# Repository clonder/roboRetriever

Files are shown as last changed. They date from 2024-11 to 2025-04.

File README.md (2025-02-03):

# 🐾 Robo Retriever

https://github.com/user-attachments/assets/8c03f9e1-ced2-4b13-8463-932fbea5f0ad

---

## 🧾 Project Description

This project aims to develop **Robo Retriever**, a four-legged robotic dog controlled via Wi-Fi, to explore and demonstrate principles of computer architecture. Using a microcontroller, we will program the robot to execute movement commands, leveraging instruction cycles, control signals, and memory management techniques. By building and testing the robot, our team will gain hands-on experience with embedded systems, hardware interfacing, and real-time data processing.

---

## 📢 Project Information

- **References**:
  - [ESP32 Small Robot Dog on Instructables](https://www.instructables.com/ESP32-Small-Robot-Dog/)
  - [PCBWay Quadruped Robot Model Introduction](https://www.pcbway.com/project/shareproject/An_introduction_to_quadruped_robot_models_0f4aa139.html)

---

## 📦 Components

| **Name** | **Description** | **Amount** | **Price** | **Link** |
|---|---|---|---|---|
| Servo Motors | Motors for robot leg movement | 12 | 60CHF | [Amazon Link](https://www.amazon.de/-/en/dp/B09WQYPP17?_encoding=UTF8&th=1) |
| Timing Belts | 25cm belts for leg motion | 4 | 6CHF | [Amazon Link](https://www.amazon.com/Cyrank-Printer-Accessories-Synchronous-MendelMax/dp/B0CH17YFQL) |
| ESP32 | Microcontroller for control | 1 | 15CHF | [Amazon Link](https://www.amazon.de/-/en/diymore-Nodemcu-Development-Bluetooth-2-ESP32/dp/B0D9BTQRYT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) |
| Battery (Akku) | Powers ESP32 and servos | 1 | - | [Amazon Link]() |
| Servo Shield | Connects ESP32 to servos and distributes power | 1 | - | [Servo Shield Link](https://www.pcbway.com/project/shareproject/Multiple_Servo_Motor_Controller_Board_DOIT_ESP32_DEVKIT_V1_c9c8165e.html) |
| Micro USB Cable | For flashing and programming ESP32 | 1 | - | We have this |
| Non-slip Material  | Rubber or pads to keep feet stable | 4 | - | [Amazon Link]() |
| Filament | 3D printing filament | 2kg | - | [Bambulab Link](https://eu.store.bambulab.com/en-ch) |
| Screws | M3 screws in various lengths | As needed  | - | [Schraubenking.ch](https://www.schraubenking.ch/) |
| Ruthex Inserts | Inserts for securing screws | As needed  | - | No need to buy |
| Delivery | For all the items, just sum | As needed  | 15CHF | - | No need to buy |

---

For more details look at the report.

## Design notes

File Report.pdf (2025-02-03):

Universität Basel, 21.01.2025

# RoboRetriever - quadruped robot

Anastasiya Merkushova, Jiri Käser, Mathieu Groenen, Rahel Kempf Lecture "Computer Architecture" by Prof. Dr. Christian Tschudin, HS24

Abstract
In this project, our aim was to build a walking quadruped robot that can be controlled via Wi-Fi. Our four-legged robot is able to walk using servo motors and an ESP32 microcontroller. The project involved designing a 3D model of the robot and printing it, determining the circuit design and power supply, and programming the servos for the robot’s movement. The robot is capable of basic movements such as tilting, walking, standing up, and sitting down.
1. Introduction
Inspired by Boston Dynamics’ Spot and other developments in quadruped robotics, we set out to create our own quadruped robot, driven by curiosity and a desire to explore the possibilities of four-legged locomotion. This project aims to design, develop, and build a quadruped robot from the ground up, from mechanical design and electronics to inverse kinematics and programming.

Quadruped robots are interesting because they are much more agile than their wheeled counterparts. Research shows their potential in traversing uneven terrain, recovering from falls and more. To remain realistic in the scope and ambitions for our project, we set out simple and hopefully achievable goals. Our goal was to build a robot that could stand up and walk.

In this report, we will delve into our journey to achieve these goals, beginning with the 3d design, in which we had to develop mechanics that would support the movements of our robot. We also had to choose an appropriate PCB design to control 12 servos at once and supply these servos with enough power. For the leg movement, we had to calculate the inverse kinematics and implement them in our code. Finally, to be able to remotely control the robot, we had to implement WIFI connection.

2. 3D Design
In this section, we will discuss the process of designing and testing the 3D model of our robot, as well as the challenges we encountered.

2.1 Physical design
First, we had to get the mental image of the robot moving. To provide our robot with the potential to turn, walk, and stand up we decided to go with three servos per leg, giving it three degrees of freedom.

To understand successful quadruped robot designs, we compared different examples online. In the end, we decided to position the servos in a way that minimizes movement, stabilizing the robot’s center of mass. This should simplify programming because we could neglect the factor of mass shifting, though it adds complexity to the mechanical design, requiring precision belts to transfer motion to the lower leg.

2.2 Model
Once the initial design was envisioned, we needed to model it in 3D software, print it, and test it excessively. For modelling, we used Onshape, a lightweight, browser-based 3D modelling software.

2.2.1 Upper and Lower Leg Design
We first modelled the upper and lower legs, along with the knee connection using a bearing. This was done very early on so we didn’t yet have the servos as reference, to check if the part would fit. Once the servos arrived, we tested the model. The initial design had several minor defects: the servo didn’t fit, there was insufficient space for a gear to be places between servo shaft and enclosure, the screw holes and the bearing hole were too small, and the strength of the part in general was too low. The final design is shown in Figure 1.

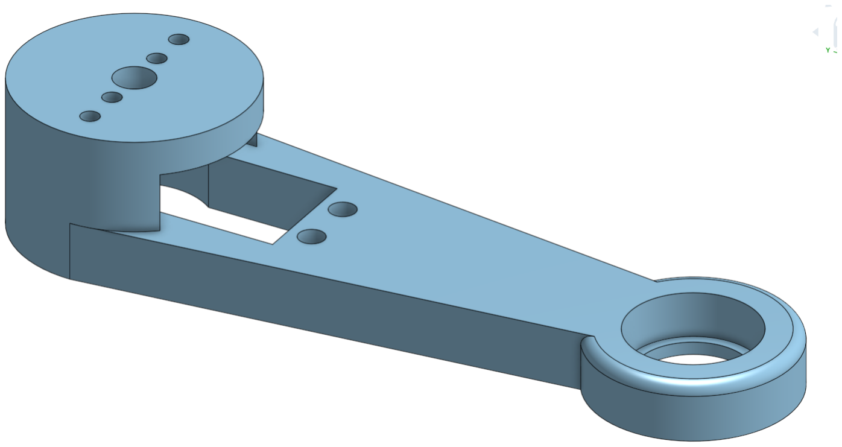
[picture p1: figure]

Figure 1. Final version of the upper leg

The lower leg had less issues but there were still a few. Issues were addressed by iterating between adjusting the 3D model according to the problems noticed during testing, reprinting and testing again. The final version of the lower leg can be seen in Figure 2.

2

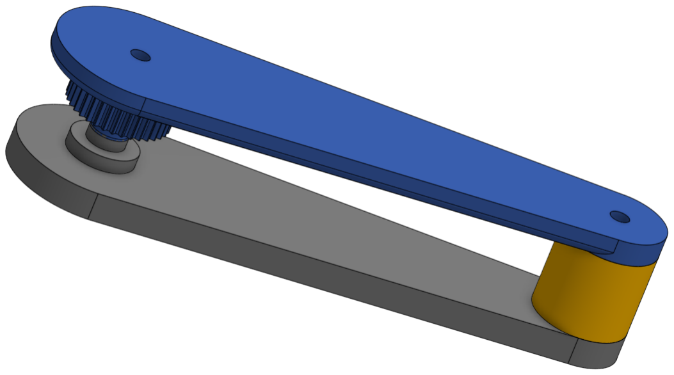
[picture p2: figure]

Figure 2. Final version of the lower leg

2.2.2 Lower Leg Motion
The next part that was addressed was the gear to drive the belt and therefore the motion of the lower leg. This part faced three main challenges: the gear needed to be compact yet strong enough to support several kilos of force, ensure the belt stayed securely in place, and have the correct gear ratio for optimal timing belt grip while keeping the height minimal.

To ensure strength, the print options were set to 6 wall layers, 50% infill, and a 0.4mm nozzle. To resolve the height issue, a new part was designed to position the servo slightly farther out, providing the extra millimeters needed for proper gear placement. Gear teeth were refined by printing 10 gears with varying teeth counts, testing, and repeating with finer increments until the optimal 35-tooth gear was selected. The final design is shown in Figure 3.

Figure 3. Final design of the gear

The final issue was belt tensioning, for which no ideal solution was found. The process went as follows:

1. A piece of timing belt was tensioned by hand hard enough not to slip any more
2. Marks for the loop closure, cut point, and overlap for sewing were added.
3. Three to four holes were punched into the belt
4. The belt was sewn together by hand with nylon string

This was the most painstaking and annoying process of assembling the robot since a little to less or too much tension meant to repeat the four steps above and they took around 20-30 minutes to complete. In the end we managed to get only two out of four running perfectly. The others worked but slipped when too much force was exerted on them. This had to then be reworked when we were in the programming phase.

2.2.3 Shoulder Design
The last two pieces needed were the shoulder, that would hold the servo rotating the upper leg and the main body holding the servos that rotate the shoulder and the electronics. The shoulder was rather straight forward as it simple needed to include a mount for the servo controlling the upper leg and a couple of holes to allow for the main body servos to control the shoulder. There were a couple of issues still, the most problematic being that one threaded insert hole was too large which caused one part of the shoulder to be ripped out during the programming phase. The final design of the shoulder can be seen in Figure 4.

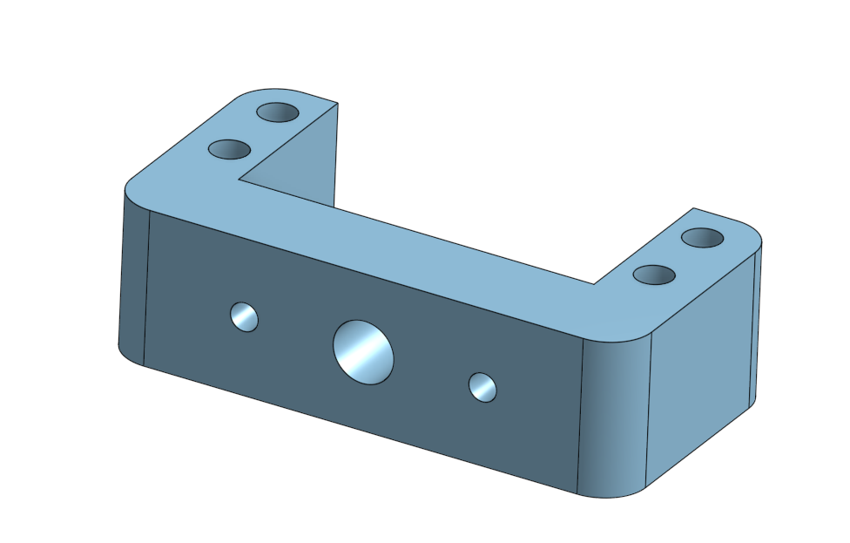
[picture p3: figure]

Figure 4. Final design of the shoulder

2.2.4 Body Design
The main body also caused a bunch of issues. We potentially wanted to power the robot by a lithium ion battery, therefore there had to be space for this, then the electronics needed to be fixed in space to make sure that cables don’t come loose easily and it needed four servo mounts while at the same time staying as light as possible. For the battery mount simply a hole in the floor was made and therefore it can be taped below the center of the main body. For the electronic mount four pillars were designed, that would hold one screw each. The problem with those was that when inserting the ruthexes these pillars would deform easily due to the low heat resistant nature of PLA Filament which made it extremely difficult to keep the correct distances for the electronic mount. The final part can be seen in figure 5.

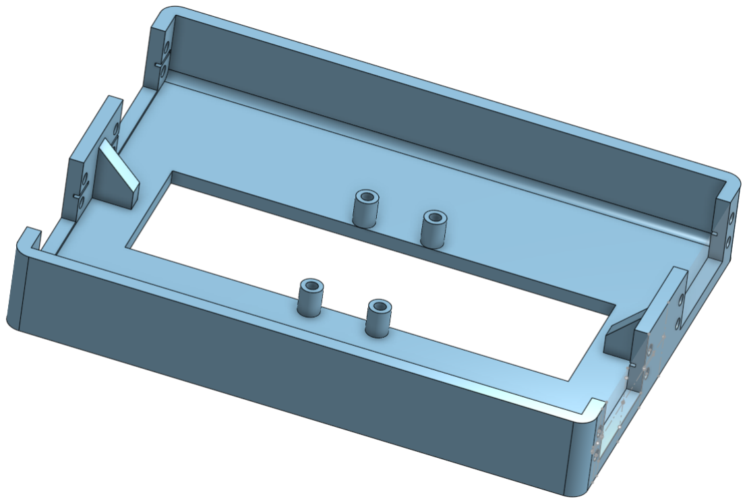
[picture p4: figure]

Figure 5. Final design of the main body

3. Electronic design
One of the core challenges in building a quadruped robot is the need to manage multiple servo motors simultaneously. The hexagonal PCB design, shown in Figure 6, was chosen

Universität Basel | 3

because it is designed to control up to 16 servo motorsa
This PCB accommodates an ESP32 microcontroller (ESP32-WROOM-32 DevKit V1b
), which features built-in Wi-Fi capabilities and allows for seamless control of the robot’s operations. The ESP32 can be powered through its USB port (5V), VIN pin, or its 3.3V regulator.

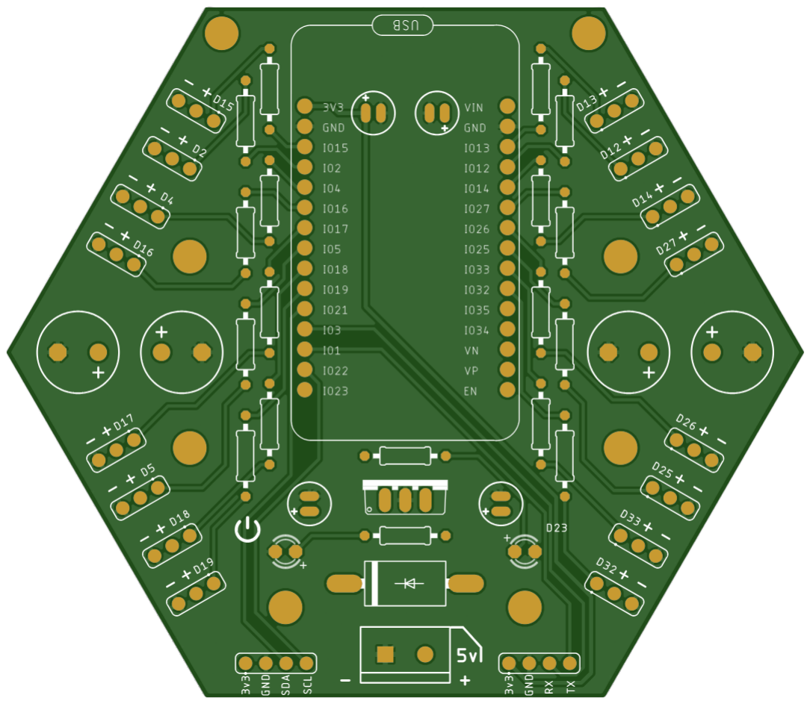
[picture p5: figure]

Figure 6. Hexagonal PCB design for servo motor control

3.1 PCB and Power
The PCB was assembled with the necessary components, including connectors, resistors, and capacitors. For the robot, we used 12 servo motors (DIYmore DM996 model), which operate at a voltage range of 4.8 V to 6.0 V, with optimal performance at 6.0 V.

Since the ESP32 operates at 5V using VIN pin, and the motors perform optimally at 6V, we opted to power the ESP32 directly via USB. For the servo motors, we used two power supplies connected in parallel: a 3-channel 5 V supply rated at 4 A and a single-channel 5 V supply rated at 4 A, providing a total current capacity of 8 A. This setup provided sufficient power to meet the robot’s peak requirements, as each servo motor has a peak current draw of 500 mA.

4. Inverse Kinematics
In this part, we explore the calculations needed for the inverse kinematics of the robot. Inverse kinematics works by choosing the location of the leg specified by its coordinates (x, y, z) and calculating the angles needed to move the leg to these coordinates. The complete leg movement is thus described by the function (θh, θs, θw) = Fθ(x, y, z). Our calculations are based on the calculations described in the OpenQuadruped project c
, with some changes made
due to differing leg design.
a. PCB design (https://www.pcbway.com/project/shareproject/Multiple_Servo_Motor_Controller_Board_DOIT_ESP32_DEVKIT_V1_c9c8165e.html)
b. ESP32 Pinout Reference (https://lastminuteengineers.com/esp32-pinout-reference/)
c. https://www.adhamelarabawy.com/images/IK_Model.pdf

4.1 Derivation
In general, we know the coordinates x, y, z which are specified by the starting condition. Additionally, SL (Shoulder length), UL (Upper leg) and LL (Lower leg) are given.

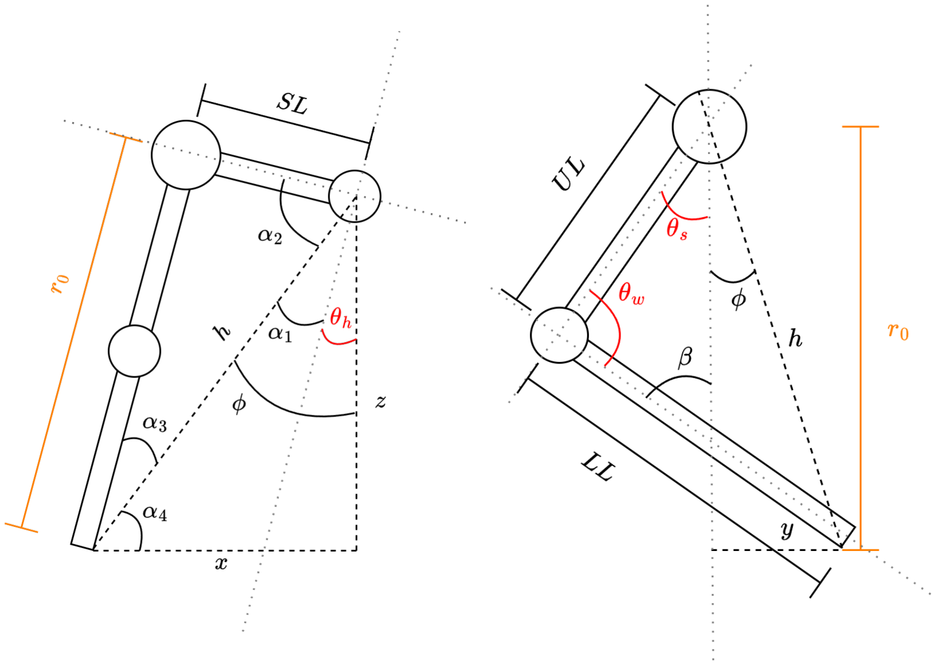
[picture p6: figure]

Figure 7. Front (left) and Side (right) view of the leg

First we look at the derivation of the θh angle as seen in figure 7, which is the angle between the body and the leg. We first calculate the distance r0.

h =

p
x

2 + z

2 ⇒ r0 =

p
h

2 − SL² =

p
x

2 + z

2 − SL²

The different angles are then given as

α2 = arccos
SL
h

α1 =

π
2

− α2

ϕ = arctan x
z

Which then gives

⇒ θh = ϕ − α1 = arctan x
z
−

π
2

+ arccos
SL
h

Now for the side view as seen in figure 7 we have

ϕ = arctan
y
r0

h =

q
r

2
0 + y

2

For θs, the shoulder angle, using the cosine law we get

cos(θs + ϕ) = UL² + h

2 − LL²
2UL · h
⇒ θs = arccos

UL² + h

2 − LL²
2UL · h

− arctan
y
r0

For θw, the knee angle, using again the cosine law

cos(θw) = UL² + LL² − h

2
2UL · LL
⇒ θw = arccos

UL² + LL² − h

2
2UL · LL

4

Thus, we get formulas for all the needed angles fully dependent on the variables x, y, z, SL, UL and LL.

Because of the design and implementation, the leg has three degrees of freedom, as depicted in figure 8. With our calculations, we are enabled to freely position the robot’s leg based on its coordinates.

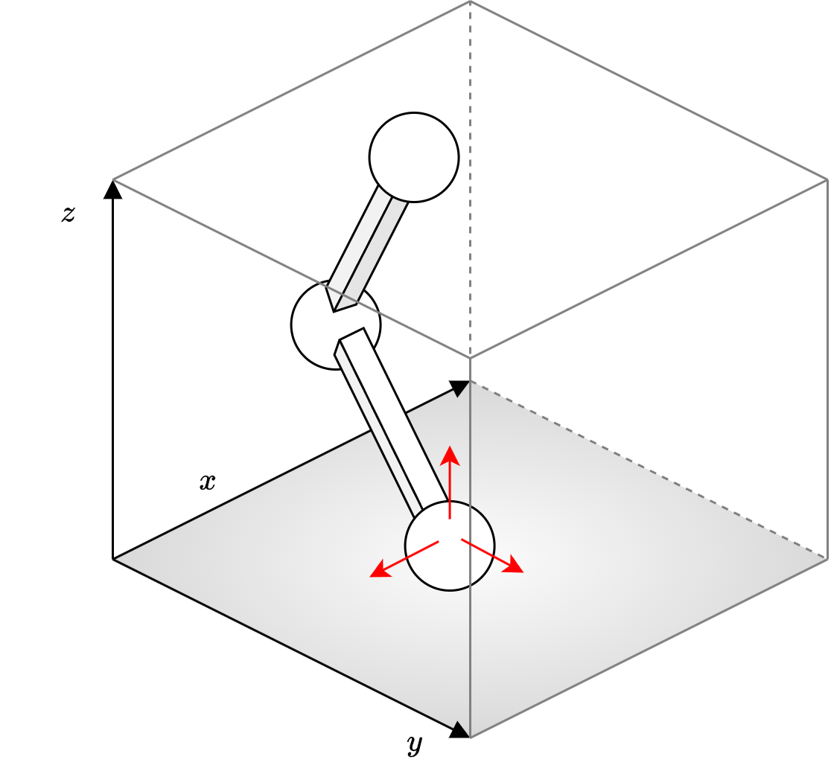
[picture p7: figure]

Figure 8. Degrees of freedom of the robot leg

5. Implementation
For programming we used an ESP32 Microcontroller, Platform.io and C++. In this section, we explain how we implemented the robot’s movements and the user interface.

5.1 Servo Positioning and Calibration
For the controlling of the servos, we use the ESP32Servo library.d The servos on the left and right side are mirroring each other, so the right side moves clockwise, while the left side moves counterclockwise. For the default positions, we had to take into consideration, that servos are only able to rotate 180 degrees. For the right side, both knee and shoulder servos are set to a default value of 0 degrees, while on the left side the default value is 180 degrees. This allows the servos on both sides to perform movements in the same range.

A large amount of time was spent correctly setting the servo angles and the positions of the legs. The need for calibration was important, as the Inverse Kinematics calculations required the correct initial placement. An offset in this placement would cause the leg to move not correct or not at all. The reason for this time-consuming part was because each time the legs needed to be recalibrated, the legs needed to be disassembled, adjusted and retested.

5.2 Movement
In this section, we describe some basic movements that the robot is capable of and how these movements are implemented. Figure 9 depicts the general architecture.
d. https://github.com/madhephaestus/ESP32Servo

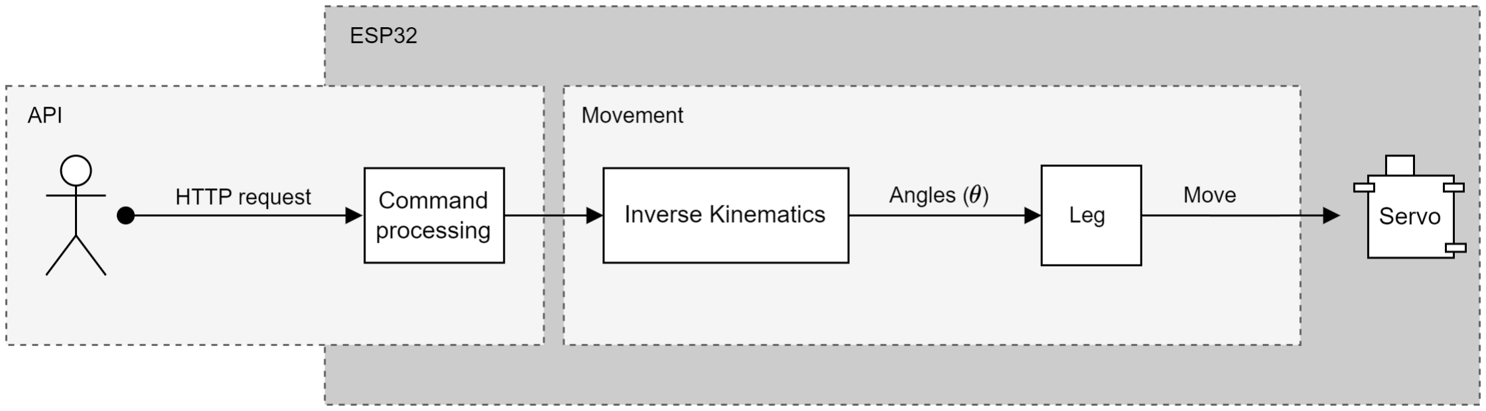
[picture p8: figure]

Figure 9. Code Architecture

5.2.1 Standing up
The robot can stand up by changing the z coordinate. The angles for this movement are calculated as described in chapter 4. With our default angles, the robot can go from 6 to 19 centimeters in height.

Standing up turned out to be harder than anticipated, as it not only depends on the correctly programmed movement but also on the stability and mechanical movement of the robot. During development, this caused a lot of problems due to the high tension and weight on the knee belts. A too quick movement of the legs would cause the knee to buckle under its own weight and would cause the robot to fall into itself. To solve this, we adjusted the movement to be incremental, such that the robot slowly moves upwards instead of one quick motion.

5.2.2 Tilting
To move the robot at an angle α in the side view (see the right image in 10) we need to specify the wanted x, y and z coordinates for each leg and based on these coordinates, calculate the needed angles. The only coordinate that changes in this movement is the z coordinate, i.e. the height of the robot.

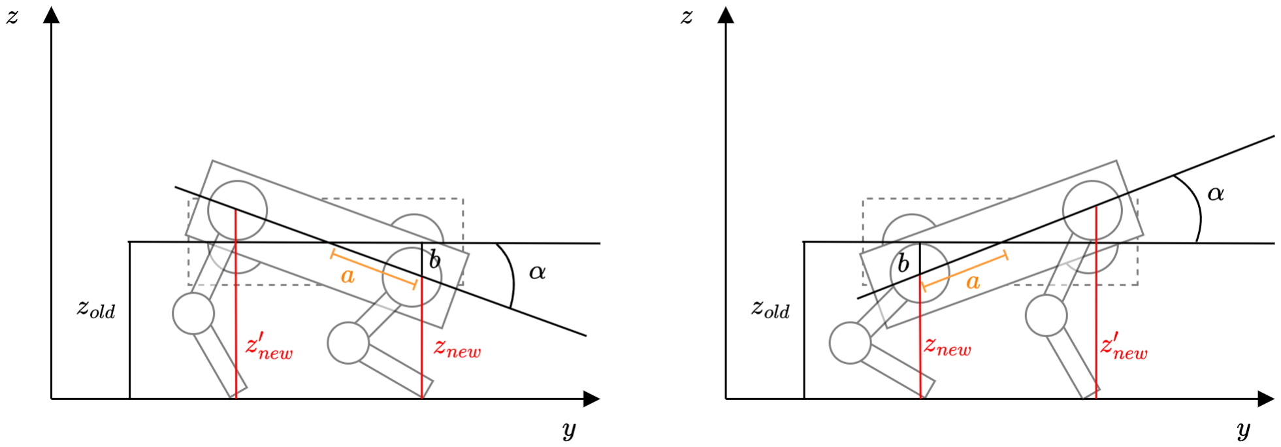
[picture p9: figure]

Figure 10. Side view of body tilting movement

b = a sin(α)

⇒znew = zold − b
⇒z

′
new = zold + b

We can then calculate the new angles for each leg. For the hind leg, the angle calculation becomes (θ

′
h

, θ′
s

, θ′
w) =
Fθ(x, y, znew) and the front legs (θ

′
h

, θ′
s

, θ′

w) = Fθ(x, y, z′
new).

5.2.3 Walking
To be able to walk, the robot needs to not only move the leg forward, but lift it up from the ground. For the

Universität Basel | 5

walking motion, we implement a parametrized curve.

γ1(t) =
t
0.05t

2

; −3 ≤ t < 3

γ2(t) =
| t − 6

1.281 cos(t − 6) + 1.718
; 3 ≤ t ≤ 9

The curves γ1(t) and γ2(t) then together define the walking motion of the robot, which can be seen in figure 11. The legs move along this curve clockwise. This curve was discretized, and the robot leg moves along the points in a certain timeframe. The leg starts at y = 0, moves clockwise and completes the movement in one iteration.

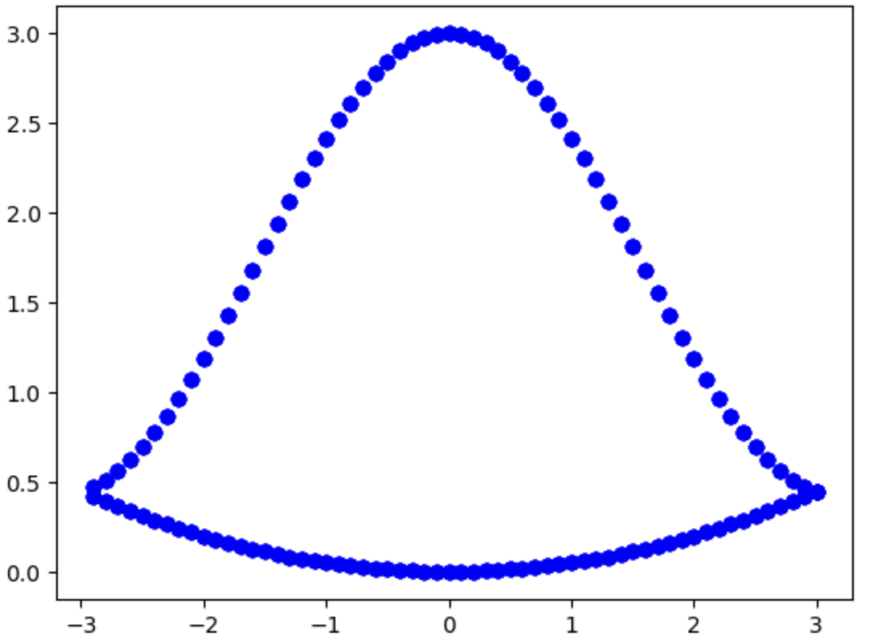
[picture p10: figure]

Figure 11. Parametrized curve of walking motion

It is important to note, that while the walking motion has been tested and works, there are still issues with the robot holding itself up due to improper balance.

5.3 User Interface
The robot’s control interface is implemented through a WiFi-enabled web server running on the ESP32 microcontroller. The system creates a wireless access point that allows for remote control of the robot’s movements via HTTP requests. Multiple commands can be chained together using semicolon separators, enabling complex movement sequences. The system implements automatic Wi-Fi reconnection and error handling to ensure reliable operation during extended use.

Table 1. Command Table

Command | Value | Function
z | 6-19 (cm) | Move vertically
y | -19-19 (cm) | Move forward/backward
bt | Angle | Tilt backward
ft | Angle | Tilt forward
w | Steps | Walk x steps forward
6. Conclusion
Our team successfully tackled an ambitious and engaging project. We gained valuable knowledge in quadruped robotics, electronics, and servo programming. Despite various challenges, we successfully completed our project and created a robot capable of executing basic commands, including walking.

6.1 Future Work
For future iterations of this project, several improvements could be implemented:
Power Supply: It would be beneficial to replace the current setup with a rechargeable battery for improved portability.
Mechanical Design: The printed parts could be revised to improve stability, and optimizing weight distribution would enhance the robot’s performance. Additionally, upgrading to wider belts with better tension mechanisms would support the robot’s weight more effectively. Software: Implementing additional movement commands would expand the robot’s capabilities and allow for more complex actions.
Project Management: Developing a more detailed project timeline, with careful consideration of dependencies between phases, would improve the project flow.

6.2 Division of Labor
Together we started planning the project, researched the topic, and decided on the required components. We distributed the work evenly, with each team member having specific areas of responsibility as outlined below. All team members contributed to the robot’s assembly and testing phases.
Anastasiya: PCB soldering, Wi-Fi interface
Jiri: 3D model design and development
Mathieu: Inverse kinematics calculations, leg movement programming
Rahel: Robot leg movement programming, Calibration

Appendix
Images
All figures depicted in this project report were self made. The 3D models are screenshots from during the design model. All other graphs were made using draw.io.

Material
All the most relevant materials used in the project can be found below
1. ESP32 WROOM 32 [Link] (https://www.amazon.de/-/en/diymore-Nodemcu-Development-Bluetooth-2-ESP32/dp/B0D9BTQRYT?nsdOptOutParam=true)
2. ESP32 Servo Control PCB [Link] (https://www.pcbway.com/project/shareproject/Multiple_Servo_Motor_Controller_Board_DOIT_ESP32_DEVKIT_V1_c9c8165e.html)
3. Servo motors [Link] (https://www.amazon.de/-/en/diymore-Gearbox-Helicopter-Aeroplane-Suitable/dp/B09WQYPP17?nsdOptOutParam=true)
4. Timing Belt [Link] (https://www.amazon.de/-/en/SIENOC-GT2-6-Open-Timing-Printer/dp/B06XX75JLV?nsdOptOutParam=true)
5. 3D fillament [Link] (https://eu.store.bambulab.com/en-ch/collections/pla/products/pla-basic-filament?variant=43923829129435)
6. Nylon string
7. Screws
8. Electrical parts (Resistors, Capacitors, Cables, Headers)

Code
All the relevant code can be found on the github repository.e All code was self-written, and ChatGPT was used as an additional tool to help with optimization and debugging of the code.
e. https://github.com/clonder/roboRetriever

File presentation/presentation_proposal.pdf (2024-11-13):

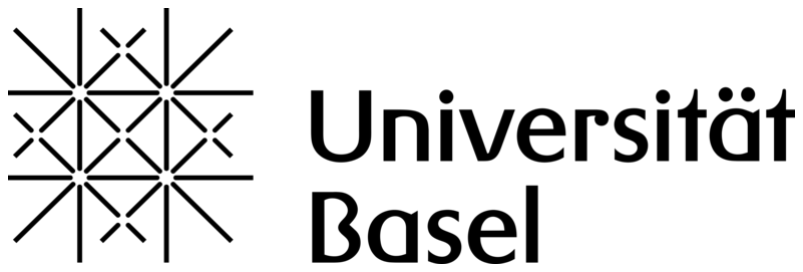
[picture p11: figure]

# Project Proposal Robo Retriever

## Computer Architecture

### A. Merkushova, J. Käser, M. Groenen, R. Kempf

Fall 2024

# Aim and goals

### - Aim:

- Develop a quadruped four-legged robotic pet controlled via Wi-Fi

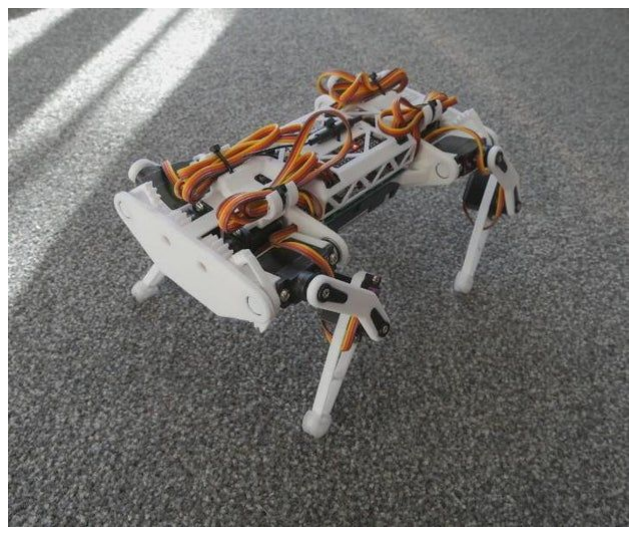
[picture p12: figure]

- Goals:
- Design Part and CAD Modeling
- 3D Printing of Parts
- Assembly
- Programming and Implementation

# Requirements

## Requirements

- ESP 32 - 38 pin with Wifi and Bluetooth
- BreadBoard / PCB
- 12 Servo Motors for movement
- Battery Holder / Batteries for power
- 3D Printing for casing

Hardware

- C / C++ for robot control
- ESP32Servo library
- Wifi.h library
- AsyncTCP.h library
- Python for remote interface

Software

# Planning

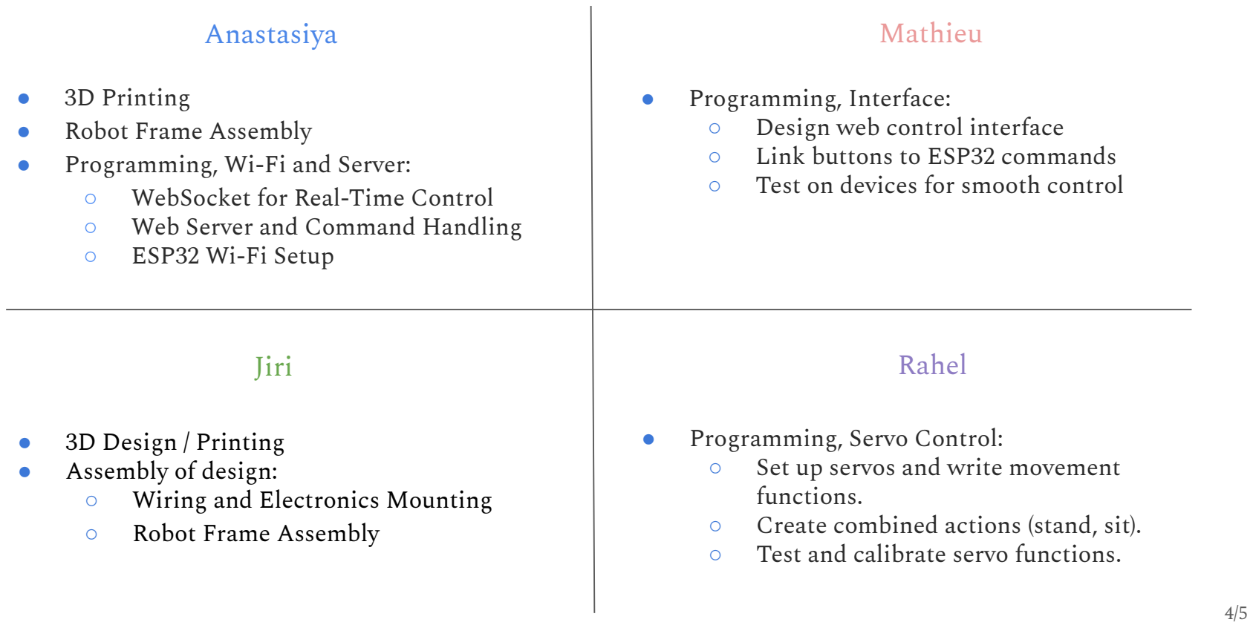
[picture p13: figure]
Mathieu; Jiri; Anastasiya; Rahel; ● 3D Printing ● Robot Frame Assembly ● Programming, Wi-Fi and Server: ○ WebSocket for Real-Time Control ○ Web Server and Command Handling ○ ESP32 Wi-Fi Setup; ● Programming, Servo Control: ○ Set up servos and write movement functions. ○ Create combined actions (stand, sit). ○ Test and calibrate servo functions.; ● 3D Design / Printing ● Assembly of design: ○ Wiring and Electronics Mounting ○ Robot Frame Assembly; ● Programming, Interface: ○ Design web control interface ○ Link buttons to ESP32 commands ○ Test on devices for smooth control

# Timeline

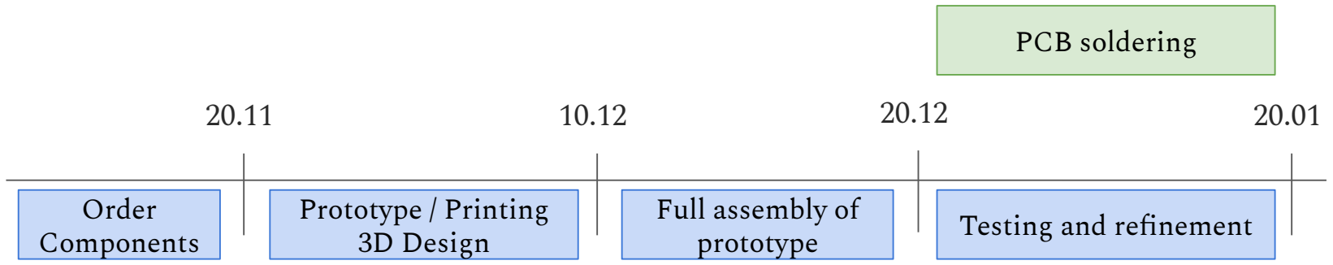
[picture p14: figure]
Order Components; Prototype / Printing 3D Design; Full assembly of prototype; Testing and refinement; PCB soldering

GUI design and
socket connection
Model servo
movement

Setup full Wifi
connection

Prototype circuit

Optional

Required

Possible additions

# Questions ?

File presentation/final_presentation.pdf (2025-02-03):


# Robo Retriever

## Computer Architecture Project

A. Merkushova, J. Käser, M. Groenen, R. Kempf

Fall 2024

# Aim and goals

- Goal:
- Develop a quadruped four-legged robotic pet controlled via Wi-Fi
- Steps:
- Design parts and print them
- Design electronics and solder
- Assembly and calibration
- Programming

# Jiri: 3D Design

### - Legs - Shoulder - Main body

# Jiri: Robot Mechanics

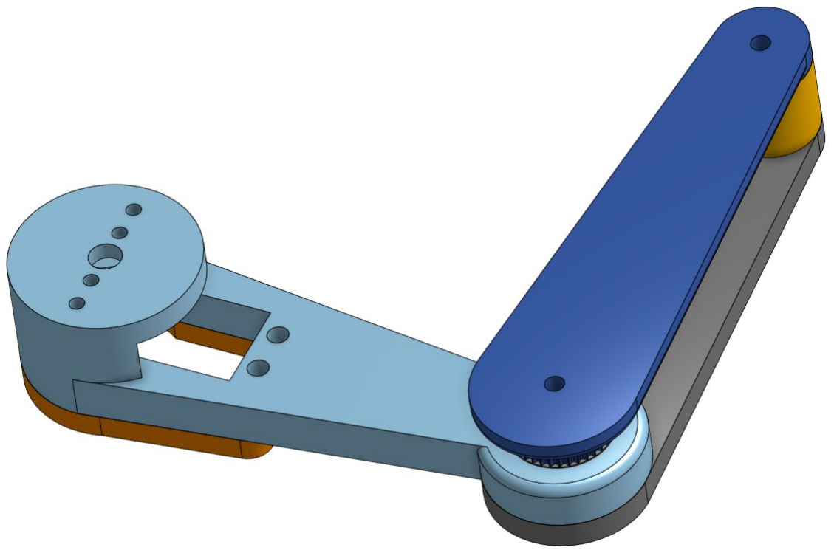
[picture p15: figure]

# Jiri: Robot Mechanics

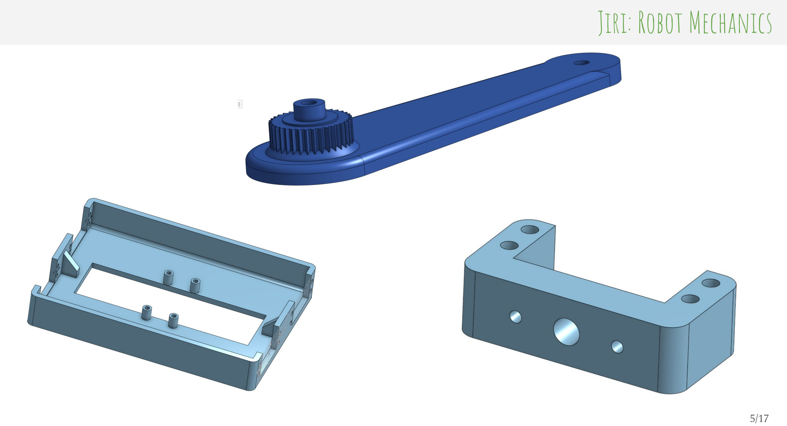
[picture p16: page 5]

# Jiri: Problems While Designing

### - Too perfect fit - Not good enough fit - Belt slipping - Servo mount slightly off - Belt distance management

- …

# Anastasiya: Electronics

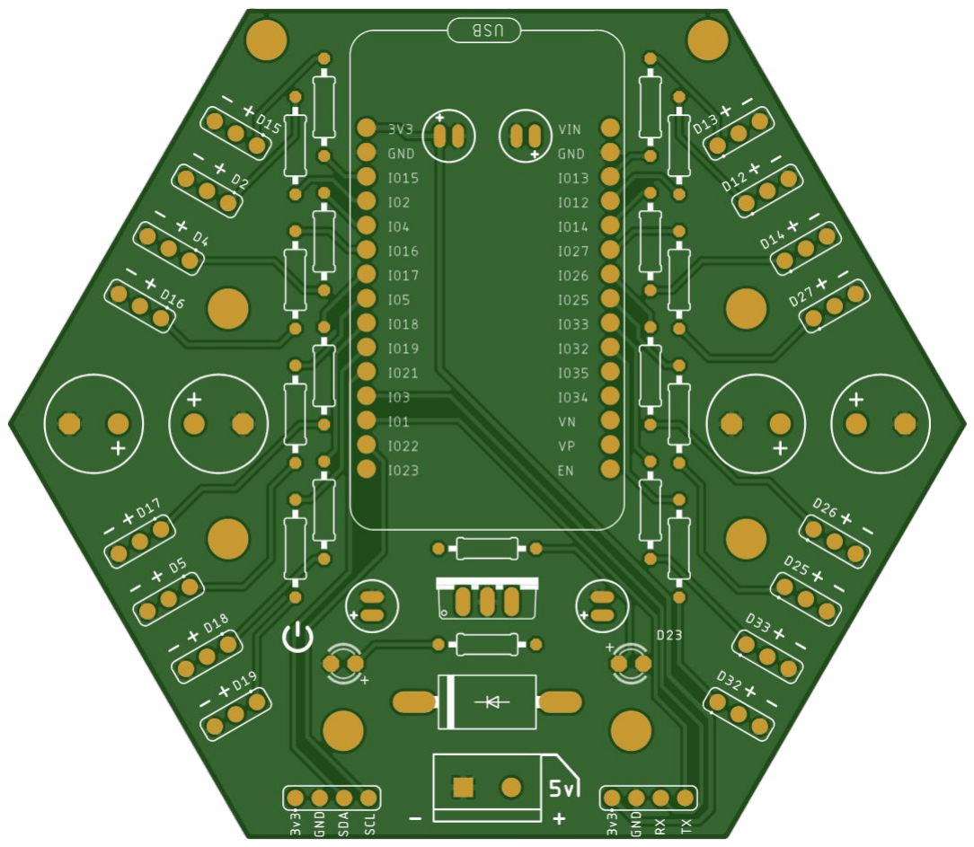
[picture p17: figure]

# Anastasiya: Electronics

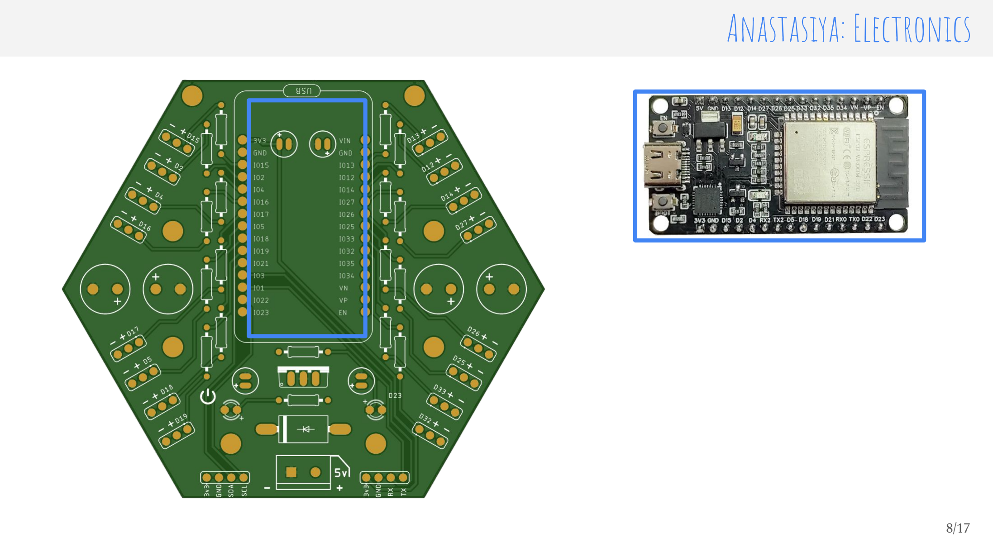
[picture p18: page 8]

# Anastasiya: Electronics

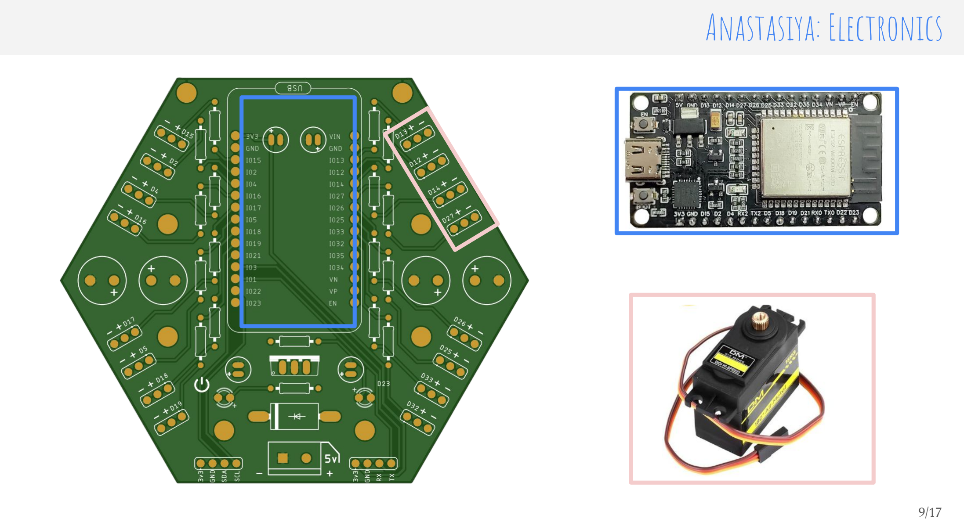
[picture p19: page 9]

# Anastasiya: Electronics

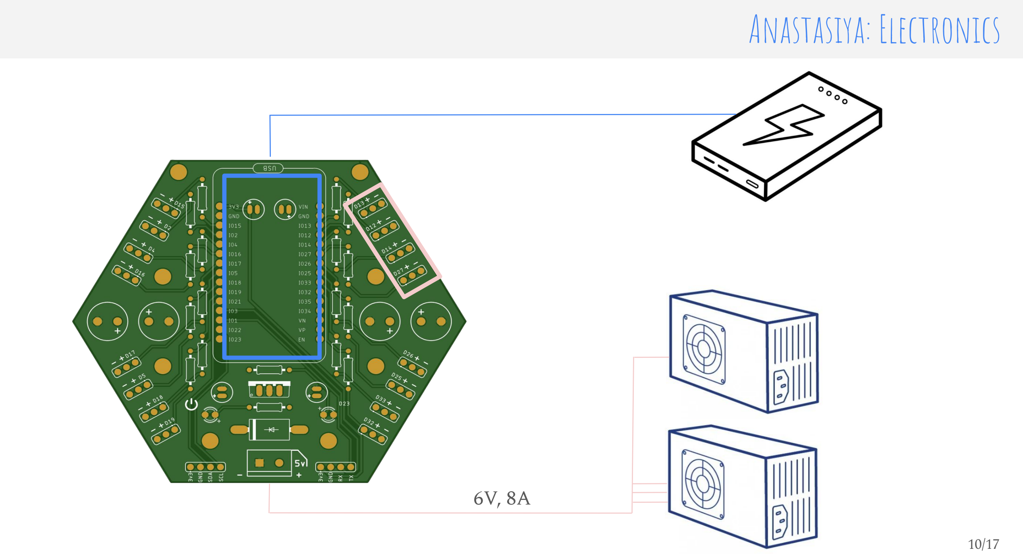
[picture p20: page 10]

6V, 8A

# Mathieu: Movement & Coding

Inverse Kinematics
- Leg movement by specifying the desired coordinates (x, y, z) and calculating the angles.

Implementation
- Implemented in C++
- Angle calculations

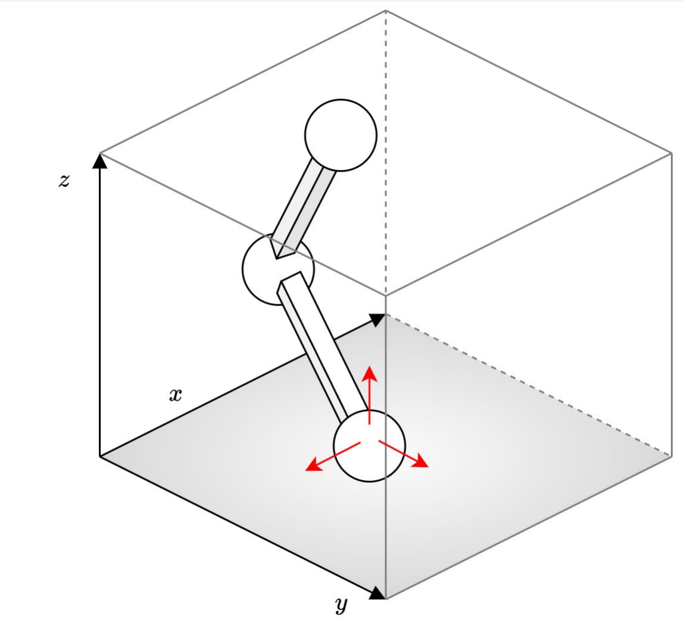
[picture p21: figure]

- Each leg governs over its servos, allowing for individual movement

Wi-Fi

- Async HTTP Server for remote control of the robot

# Mathieu: Code Architecture

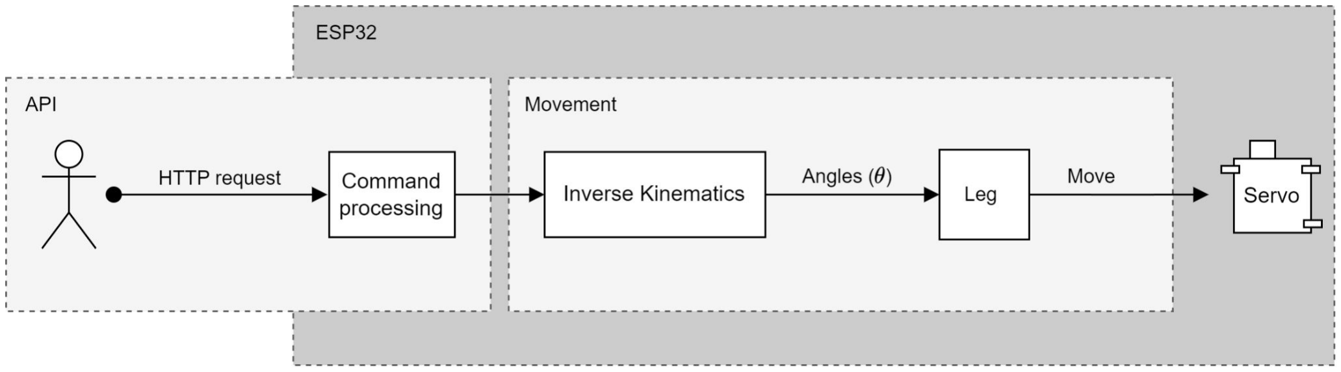
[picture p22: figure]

### - Stand up / Sit - Tilt forward and backwards - Walk forwards

# Rahel: DEMO

# Rahel: Tilting

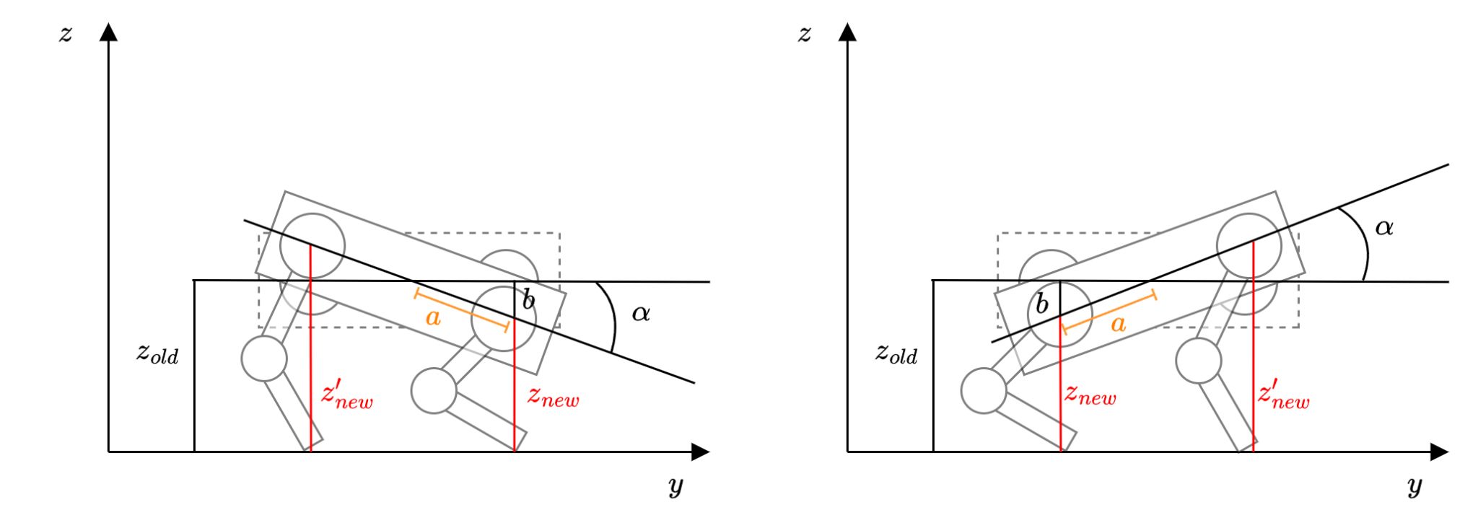
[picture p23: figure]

# Rahel: Walking

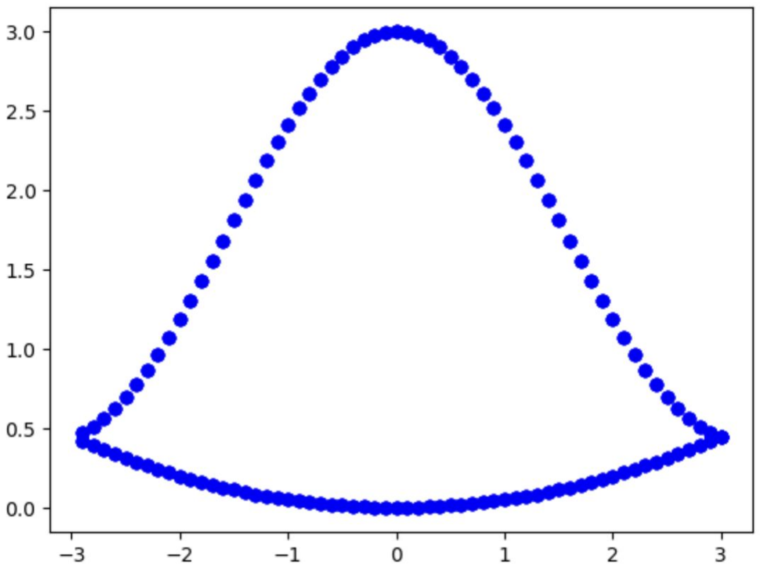
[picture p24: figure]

# Conclusion

- Results:
- Functional 3D design
- Electronic setup capable of controlling multiple servos
- Basic movement
- Future Work:
- Refine 3D design for stability
- Include rechargeable battery
- Optimize walking
- Remote Control with Interface

# Questions ?

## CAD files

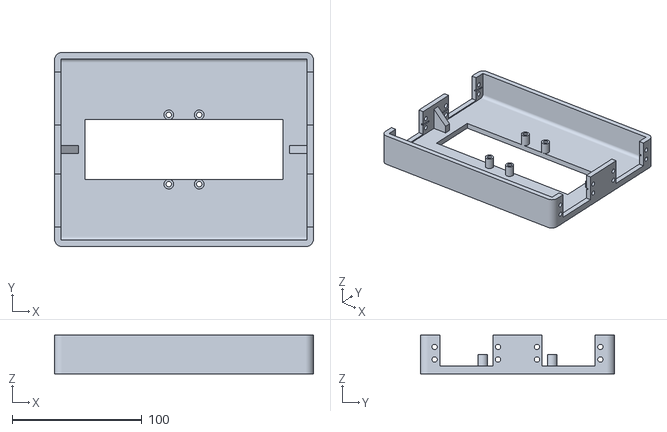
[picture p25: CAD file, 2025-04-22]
cad/body - MainBody.stl
200.0 x 150.0 x 30.0

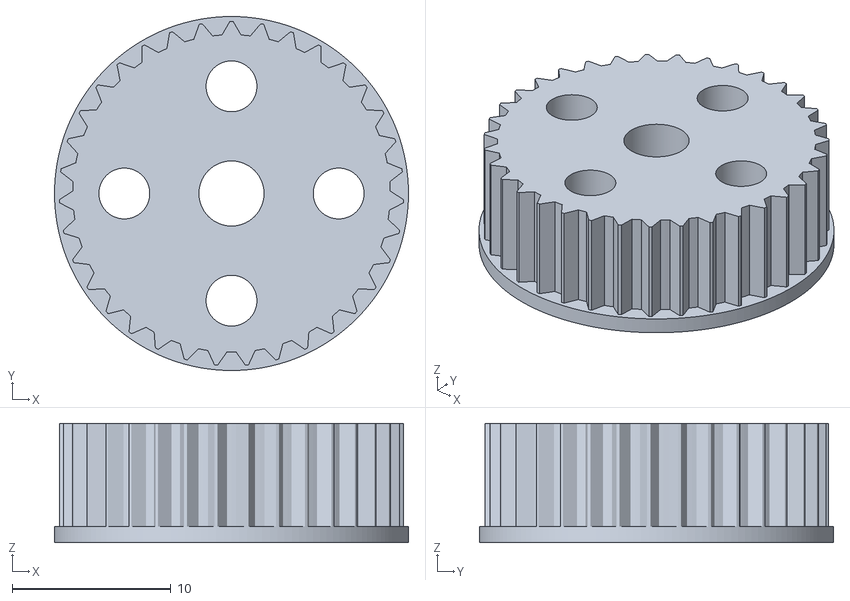
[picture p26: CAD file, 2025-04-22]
cad/arm - Gear.stl
22.3 x 22.3 x 7.50

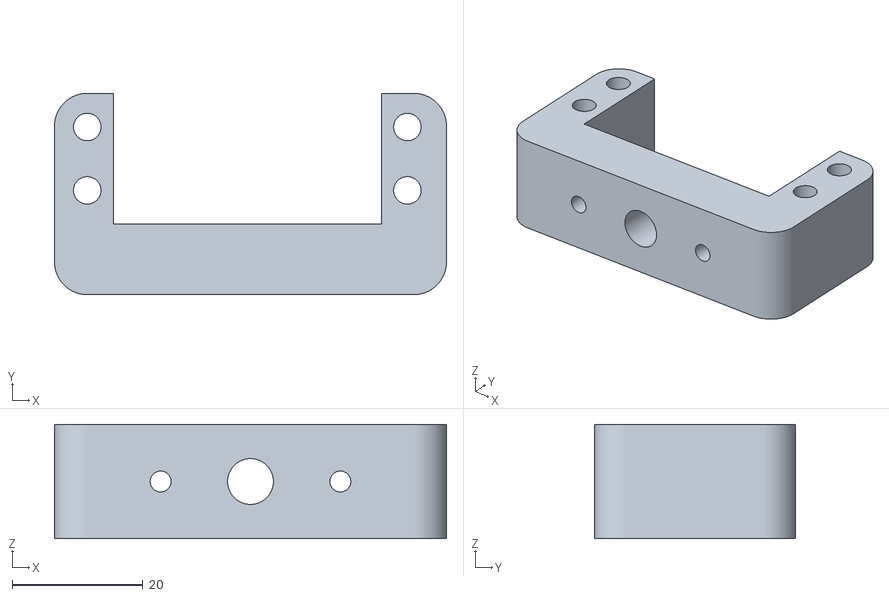
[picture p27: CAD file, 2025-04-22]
cad/shoulder - Shoulder.stl
60.0 x 30.8 x 17.5

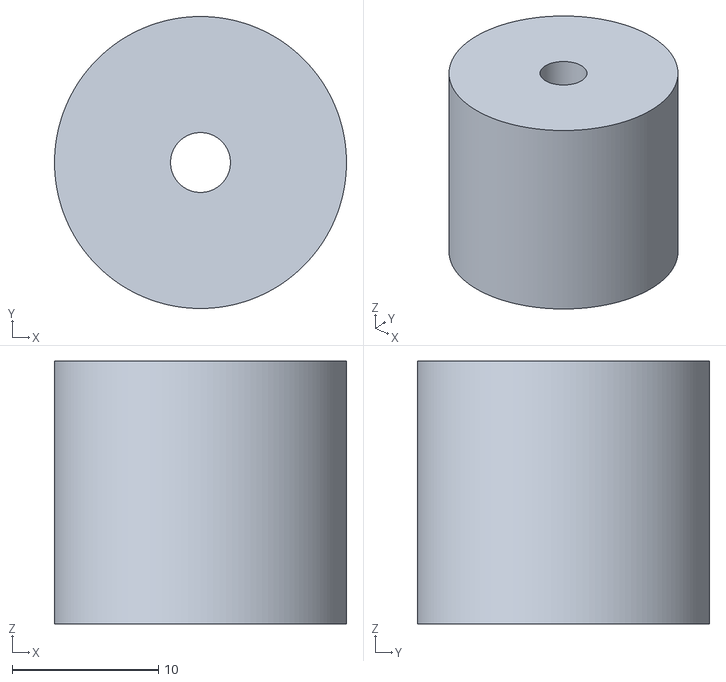
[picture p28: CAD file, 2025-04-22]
cad/arm - splitter.stl
20.0 x 20.0 x 18.0

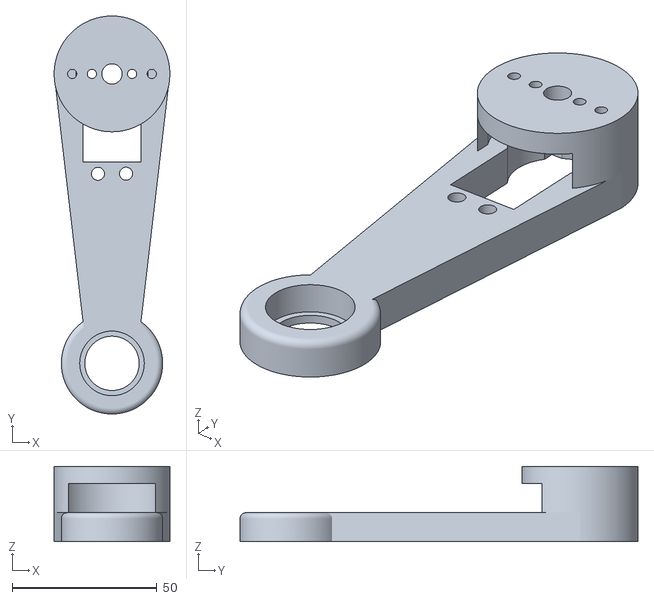
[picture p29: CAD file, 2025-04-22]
cad/arm - Oberschenkel.stl
40.0 x 137.5 x 26.0

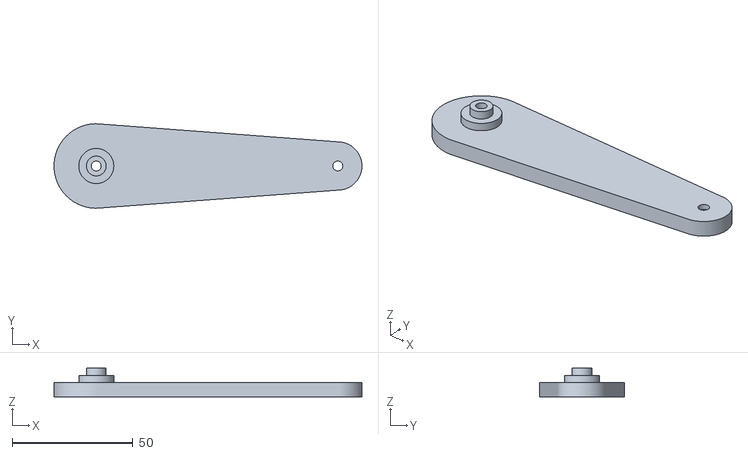
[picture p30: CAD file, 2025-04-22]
cad/arm - UnterschenkelDeckel.stl
127.5 x 35.0 x 12.0

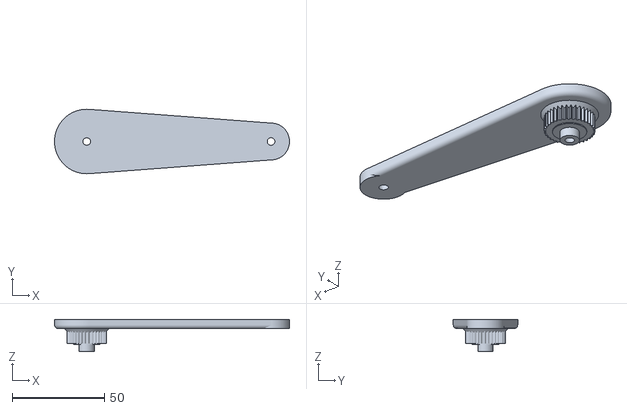
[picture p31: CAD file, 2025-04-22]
cad/arm - Unterschenkel.stl
127.5 x 35.0 x 17.5

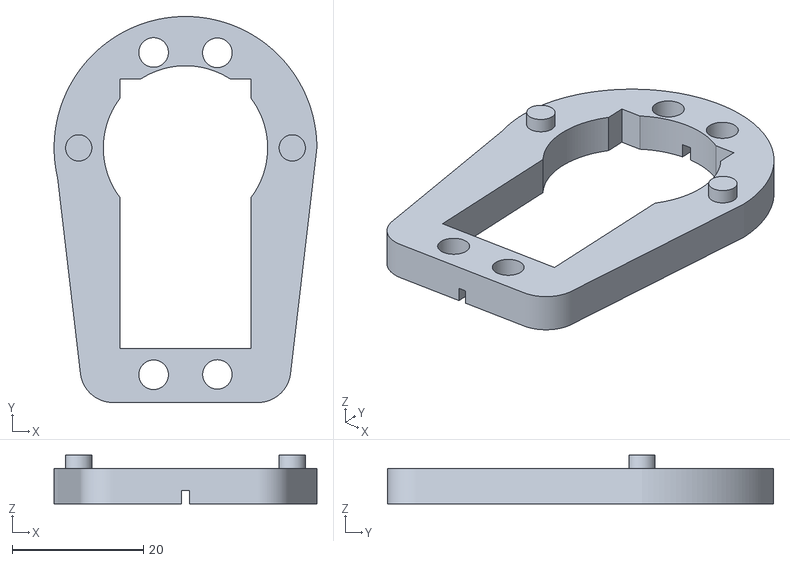
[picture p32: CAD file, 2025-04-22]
cad/arm - servoHeber.stl
40.0 x 58.7 x 7.40

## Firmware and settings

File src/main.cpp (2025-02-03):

#include <Controller.h>
#include <InverseKinematics.h>
#include <string>
#include <WiFi.h>
#include <ESPAsyncWebServer.h>
#include <vector>
#include "esp_task_wdt.h"

using namespace std;

const char *ssid = "Clonder";
const char *password = "1234567812";

AsyncWebServer server(80);
InverseKinematics ik;
bool wifiConnected = false;

void setup()
{
    // Setup serial
    Serial.begin(115200);
    while (!Serial)
    {
    }

    // Initialize watchdog timer
    esp_task_wdt_init(120, true);

    // Connect to Wi-Fi
    WiFi.begin(ssid, password);
    unsigned long startAttemptTime = millis();
    while (WiFi.status() != WL_CONNECTED && millis() - startAttemptTime < 10000)
    {
        delay(1000);
    }

    if (WiFi.status() == WL_CONNECTED)
    {
        wifiConnected = true;
    }

    // Position servos into default position
    ik.Start();
    delay(1000);

    server.on("/test", HTTP_GET, [](AsyncWebServerRequest *request)
              { request->send(200, "text/plain", "Test endpoint reached"); });

    server.on("/command", HTTP_GET, [](AsyncWebServerRequest *request)
              {
        if (request->hasParam("cmd")) {
            String command = request->getParam("cmd")->value();
            string data = command.c_str();
            // Split the commands by semicolon
            vector<string> commands;
            size_t pos = 0;
            while ((pos = data.find(";")) != string::npos) {
                commands.push_back(data.substr(0, pos));
                data.erase(0, pos + 1);
            }
            commands.push_back(data);

            // Execute each command
            for (const string& cmd : commands) {
                // command for moving along y-axis (for/backwards)
                if (cmd.find("y") != -1) {
                    int y = stoi(cmd.substr(1, cmd.length()));
                    ik.moveY(y);
                // command for walking
                } else if (cmd.find("w") != -1) {
                    int steps = stoi(cmd.substr(1, cmd.length()));
                    for (Leg *leg : ik.legs) {
                        if (leg->isHind) {
                            ik.moveY(leg, -10);
                        }
                        else {
                            ik.moveY(leg, -6);
                        }
                        leg->calculateCurve(); // saves array of points for walking interpolation
                        leg->calculateInterpolationAngles();                        
                    }
                    //ik.moveZ(Constants::WALKINGHEIGHT);
                    for (int i = 0; i < steps; i++) {
                        ik.moveForward();
                    }
                    esp_task_wdt_reset();
                // command for moving vertically
                } else if (cmd.find("z") != -1) {
                    int z = stoi(cmd.substr(1, cmd.length()));
                    if (z >= 6 && z <= 19) {
                        // Get current z of first leg, as all legs have same height;
                        int current_z = ik.legs[0]->z;
                        int step = z > current_z ? 1 : -1;
                        // Incrementally move z position
                        for (int i = current_z; i != z; i += step) {
                            ik.moveZ(i);
                            delay(10);
                        }
                    }
                // command for tilting forward
                } else if (cmd.find("ft") != -1) {
                    int a = stoi(cmd.substr(2, cmd.length()));
                    if (a >= -1000 && a <= 1000) { //TODO: adjust
                        ik.tilt(a, FORWARD);
                    }
                // command for tilting backward
                } else if (cmd.find("bt") != -1) {
                    int a = stoi(cmd.substr(2, cmd.length()));
                    if (a >= -100 && a <= 100) { //TODO: adjust
                        ik.tilt(a, BACKWARD);
                    }
                // command for resetting to starting position
                } else if (cmd.find("RESET") != -1) {
                    ik.Start();
                } else {
                    request->send(400, "text/plain", "Invalid command: " + String(cmd.c_str()));
                    return;
                }
                delay(500);
            }
            request->send(200, "text/plain", "Command sequence executed");
        } else {
            request->send(400, "text/plain", "No command sent");
        } });

    server.begin();
}

void loop()
{
    // Attempt to connect to WiFi until connected
    if (!wifiConnected)
    {
        WiFi.begin(ssid, password);
        unsigned long startAttemptTime = millis();

        // Wait for connection
        while (WiFi.status() != WL_CONNECTED && millis() - startAttemptTime < 10000)
        {
            delay(500);
        }

        if (WiFi.status() == WL_CONNECTED)
        {
            wifiConnected = true;
        }
        else
        {
            // If not connected, restart the attempt
            WiFi.disconnect();
            delay(1000);
        }
    }

    // Add a small delay to avoid flooding the Serial Monitor
    delay(1000);
}

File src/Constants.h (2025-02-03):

//
// Created by mathi on 29/12/2024.
//

#ifndef CONSTANTS_H
#define CONSTANTS_H

// Constants related to the body dimensions of the robot
namespace Constants
{
    constexpr double LIMB = 10.0;
    // constexpr double LOWERLEG = 10.0;
    constexpr double SHOULDER = 6.1;

    constexpr double BASEHEIGHT = 5.0;          // default z value
    constexpr double BASESIDELEGEXTEND = 0.5;   // default y value
    constexpr double BASEFRONTELEGEXTEND = 5.5; // default x value

    constexpr double HALF_BODY = 7;

    constexpr int BODYDEFAULTANGLESERVO = 85;
    constexpr int SHOULDERDEFAULTANGLESERVO = 0; // Right side
    constexpr int LEFT_SHOULDERDEFAULTANGLESERVO = 180;
    constexpr int KNEEDEFAULTANGLESERVO = 0;
    constexpr int LEFT_KNEEDEFAULTANGLESERVO = 180;

    constexpr int BODYDEFAULTANGLE = 90;
    constexpr int SHOULDERDEFAULTANGLE = 85;
    constexpr int KNEEDEFAULTANGLE = 30;

    constexpr int WALKINGHEIGHT = 13;
    constexpr int AMOUNT_POINTS = 120;
}

#endif // CONSTANTS_H

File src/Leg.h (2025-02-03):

//
// Created by mathi on 29/12/2024.
//
#ifndef LEG_H
#define LEG_H

#include <Constants.h>
#include <ESP32Servo.h>

enum Direction {
    FORWARD = 0,
    BACKWARD = 1,
};

/**
 * Holds all information related to one leg
 */
class Leg {
    public:
        bool isLeft;
        bool isHind;

        //current angles
        int kneeAngle = Constants::KNEEDEFAULTANGLESERVO;
        int shoulderAngle = Constants::SHOULDERDEFAULTANGLESERVO;
        int bodyAngle = Constants::BODYDEFAULTANGLESERVO;

        //desired angles
        int next_kneeAngle = Constants::KNEEDEFAULTANGLESERVO;
        int next_shoulderAngle = Constants::SHOULDERDEFAULTANGLESERVO;
        int next_bodyAngle = Constants::BODYDEFAULTANGLESERVO;

        // Positions
        double x = Constants::BASEFRONTELEGEXTEND;
        double y = Constants::BASESIDELEGEXTEND;
        double z = Constants::BASEHEIGHT;

        // Servos
        Servo BodyServo;
        Servo ShoulderServo;
        Servo KneeServo;

        // Walking
        std::tuple<double, double> curve_values[Constants::AMOUNT_POINTS];
        std::tuple<int, int> interpolation_angles[Constants::AMOUNT_POINTS]; // shoulder and knee angle

        /** Constructor for leg where pin numbers are passed for servo's
         * @param bodyServoPin
         * @param shoulderServoPin
         * @param kneeServoPin
         */
        Leg(int bodyServoPin, int shoulderServoPin, int kneeServoPin, bool isLeft, bool isHind)
        {
            this->isLeft = isLeft;
            this->isHind = isHind;

            calculateCurve(); // saves array of points for walking interpolation
            calculateInterpolationAngles();

            if (isLeft) {
                kneeAngle = Constants::LEFT_KNEEDEFAULTANGLESERVO;
                shoulderAngle = Constants::LEFT_SHOULDERDEFAULTANGLESERVO;

                next_kneeAngle = Constants::LEFT_KNEEDEFAULTANGLESERVO;
                next_shoulderAngle = Constants::LEFT_SHOULDERDEFAULTANGLESERVO;
            }

            BodyServo.setPeriodHertz(50);
            BodyServo.attach(bodyServoPin, 500, 2400);

            ShoulderServo.setPeriodHertz(50);
            ShoulderServo.attach(shoulderServoPin, 500, 2400);

            KneeServo.setPeriodHertz(50);
            KneeServo.attach(kneeServoPin, 500, 2400);
        }

        /**
        * Rotate knee servo
        * @param angle
        */
        void rotateKnee(int angle);

        /**
        * Rotate shoulder servo
        * @param angle
        */
        void rotateShoulder(int angle);

        /**
        * Rotate body servo
        * @param angle
        */
        void rotateBody(int angle);

        /**
         * Move the leg
         */
        void move();

        void rotateServo(Servo *servo, int angle);

        void updateCoordinates(double new_x, double new_y, double new_z);
        void updateAngles();

        void resetPosition();

        // calculates the points for the curve movement when walking
        void calculateCurve();

        // calculates the angles for each position that the leg needs to take
        void calculateInterpolationAngles();
};

#endif //LEG_H

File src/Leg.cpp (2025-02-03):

//
// Created by mathi on 29/12/2024.
//

#include "Leg.h"
#include <Arduino.h>
#include <ESP32Servo.h>
#include <InverseKinematics.h>

using namespace std;

void Leg::rotateKnee(int angle)
{
    if (isLeft)
    {
        angle = 180 - angle;
    }
    rotateServo(&KneeServo, angle);
}

void Leg::rotateShoulder(int angle)
{
    if (isLeft)
    { // left shoulder movement
        angle = 180 - angle;
    }
    rotateServo(&ShoulderServo, angle);

    // delay(10);
}

void Leg::rotateBody(int angle)
{
    rotateServo(&BodyServo, angle);
}

void Leg::updateCoordinates(const double new_x, const double new_y, const double new_z)
{
    x = new_x;
    y = new_y;
    z = new_z;
}

void Leg::updateAngles()
{
    kneeAngle = next_kneeAngle;
    shoulderAngle = next_shoulderAngle;
    bodyAngle = next_bodyAngle;
}

void Leg::rotateServo(Servo *servo, int angle)
{
    servo->write(angle);
    // delay(10);
}

void Leg::move()
{
    rotateBody(next_bodyAngle);
    rotateShoulder(next_shoulderAngle);
    rotateKnee(next_kneeAngle);
    updateAngles();
}

void Leg::resetPosition()
{
    rotateServo(&BodyServo, Constants::BODYDEFAULTANGLESERVO);
    if (isLeft)
    {
        rotateServo(&ShoulderServo, Constants::LEFT_SHOULDERDEFAULTANGLESERVO);
        rotateServo(&KneeServo, Constants::LEFT_KNEEDEFAULTANGLESERVO);
    }
    else
    {
        rotateServo(&ShoulderServo, Constants::SHOULDERDEFAULTANGLESERVO);
        rotateServo(&KneeServo, Constants::KNEEDEFAULTANGLESERVO);
    }
    updateCoordinates(Constants::BASEFRONTELEGEXTEND, Constants::BASESIDELEGEXTEND, Constants::BASEHEIGHT);
}

void Leg::calculateCurve()
{
    double multiplier = 0.1;
    tuple<int, int> bottom_range = make_tuple(-3, 3);
    tuple<int, int> top_range = make_tuple(3, 9);

    double length = get<1>(top_range) - get<0>(bottom_range);
    int amount_points = length / multiplier;

    // parametrisierte wege untere kurve [-3, 3]
    auto bottom_func = [](double i) -> tuple<double, double>
    {
        return make_tuple(-i, 0.05 * pow(i, 2));
    };

    // values obere kurve
    auto top_func = [](double i) -> tuple<double, double>
    {
        return make_tuple((i - 6), 1.281 * cos(i - 6) + 1.718);
    };

    for (int i = 0; i < amount_points; i++)
    {
        // Maps [0, 12] to [0, 9] + [-3, 0] ranges so that starting point of array is starting point of walking motion
        // f(x) = (x + 3) % 12 - 3
        double t = std::fmod(i * multiplier + 3., 12) - 3;
        if (t >= get<0>(bottom_range) && t < get<1>(bottom_range))
        {
            // calculate bottomfunc
            curve_values[i] = bottom_func(t);
        }
        else
        {
            // calculate topfunc
            curve_values[i] = top_func(t);
        }
    }
}

void Leg::calculateInterpolationAngles()
{
    // 1.
    for (int i = 0; i < Constants::AMOUNT_POINTS; i++)
    {
        tuple<double, double> curve_point = curve_values[i];
        double z_value = z - get<1>(curve_point);
        double thetaW = InverseKinematics::calculateThetaW(x, y + get<0>(curve_point), z_value);
        double thetaS = InverseKinematics::calculateThetaS(x, y + get<0>(curve_point), z_value);
        interpolation_angles[i] = make_tuple(thetaS, thetaW);
    }
}

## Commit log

2024-11-25 Added platformio.ini. CPP controller and main thread for wifi connection
2024-11-25 Added socket connection to ESP32 for python and input send format
2024-11-30 Changed controller reader. Added threading for controller reader and continious input sender over socket connection
2024-12-11 Added Inverse Kinematics diagramms and report.
2024-12-29 Added Inverse kinematics complete code and made small changes to code structure
2024-12-30 Added all leg calibration
2024-12-30 Added other leg movement
2025-01-07 y axis movement
2025-01-15 add incremental movement of servos
2025-01-17 Added incremental movement of Z axis
2025-01-21 update Angles after resetting
    [Leg.cpp]
2025-04-22 added cad files
    [arm - Gear.stl, arm - Oberschenkel.stl, arm - Unterschenkel.stl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]
